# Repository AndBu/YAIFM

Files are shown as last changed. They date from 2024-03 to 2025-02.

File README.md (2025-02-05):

# Yet another IKEA Fridans Motorization (YAIFM)

An affordable, available, easy-to-build drop-in replacement for the orginial “magic wand”. The design has been up and running in my own home for a good half year now and it works without any issues so far. The benefits are:
* Drop-in replacement, i.e. works with the same IKEA wall or ceiling mounts, no new holes or repositioning necessary
* Powered from a regular 5V USB-C power supply
* Works with Home Assistant using ESPHome
* Worldwide availability of components (through Aliexpress and/or other electronics vendors)
* 3D printable on a stock Ender 3

Here are two gifs of how to install the final product:

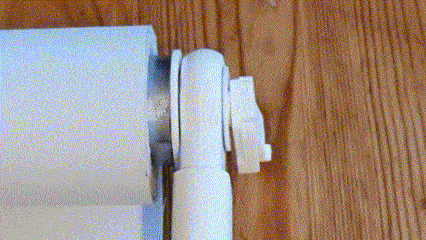
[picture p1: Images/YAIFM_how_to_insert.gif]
How to attach it.

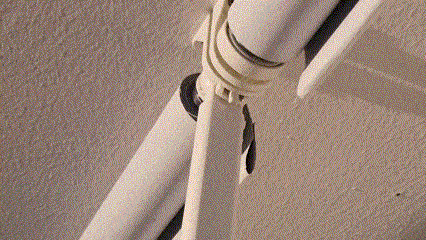
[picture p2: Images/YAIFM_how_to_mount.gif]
How to install it.


And here is a gif of it in action:

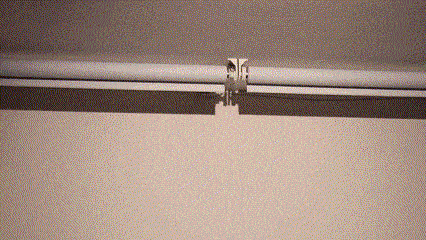
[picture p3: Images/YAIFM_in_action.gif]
How to use it.


Interested? This repository has all you need. The basic steps are simple:
1. Print the parts and assemble the motor holder (screwing required)
2. Assemble the control PCB (soldering required)
3. Flash ESPHome and integrate everything within HomeAssistant
4. Remove the wand, pop in the motor assembly, connect the wires
5. Profit

So you have set you mind on building this things? Awesome! **Be sure to check out the [Limitations and constraints](#limitations-and-constraints) section at the end of this document before you start.**

# Bill of Materials (BOM)

For building one device, you will need to first obtain all the parts on the Bill of Materials (BOM) in the listed quantities. The BOM is separated in to everything needed for the motor assembly as well as everything needed for the control electronics and the wiring.

You can download a Microsoft [Excel file of the BOM here](https://github.com/AndBu/YAIFM/blob/main/BOM/YAIFM%20Bill%20of%20Materials%20(BOM).xlsx).

## Motor assembly BOM

The motor assembly houses the motor and is equipped with an optional wned stop switch to detect the blind's end stop position. **Please be aware, that while a version without an endstop switch exists, I have not yet created a yaml-script for that**. The motor assembly is the part that gets fit into the pipe instead of the "magic wand". The components needed for the motor assembly are listed below:

| Component | Description | Supplier | Alternative | Quantity | Cost (app.) |
| --- | --- | --- | --- | --- | --- |
| Motor holder | Due to the general limitations of FDM 3D printing, the motor assembly is split into multiple parts: the motor holder, the lid and the clip. An optional switch holder can be attached for using en end-stop switch for the blinds. | 3D printed | \- | 1x | \- |
| Motor holder lid | Lid for motor holder. | 3D printed | \- | 1x | \- |
| Motor holder clip | The clip is used to snap the motor assembly in place, much like the original wand. The clip has to be printed in a different orientation for easy printing and maximum mechanical stability, so it is a separate part. | 3D printed | \- | 1x | \- |
| M3x4mm flat head screw | The orignal IKEA Fridans wand is rivited. My clip is screwed onto the motor holder with a flat M3x4mm screw. The screw's maximum head thickness is 1.5mm. You can probably get away with a thicker screw or just glue it. | [Aliexpress](https://www.aliexpress.com/item/1005004288328345.html) | Hardware store | 1x | 1USD (per set) |
| DC motor | GA12-N20 miniature geard DC motor wth integrated rotary encoder, with 39RPM @ 6V supply. Different version of this motor exist with different power and torque rating. In order to reliably drive the widest (200cm) IKEA Fridans blinds, I recommend a motor with a stall torque of at least 0.5Nm and a shaft speed of around 39RPM at no load. Be careful, motors can have different electrical characteristics even though they look the same. The Adafruit motor is slower and on the lower end of the torque spectrum. It won't work reliably for blinds >100cm (and even for the narrower blinds, I have not tested it), but I have included it, because it might be easier to source for some of you. | [Aliexpress](https://www.aliexpress.com/item/4001045242610.html?spm=a2g0o.order_list.order_list_main.196.54af1802pgRf9I) | [Adafruit (not for >100cm blinds!)](https://www.adafruit.com/product/4640) | 1x | 10 USD |
| Hub | The hub sit directly on the motor shaft and transfers the torque from the gearbox to the blind. It should fit rather firmly. I have included multiple parts with different shaft tolerances and I have also included a tolerance tester part so you can choose the right part before printing the whole hub. | 3D printed | \- | 1x | \- |
| Switch holder | Optional. The switch holder secures the limit switch at the correct angle and distance. The switch holder is long because the plastic reinforcement inside the seam of the blind's fabric triggers switch and it can move. If you have an unusually short reinforcement part, for example because you were not careful when cutting your blinds to fit, you might need to make adjustments to this part. | 3D printed | \- | 1x | 5USD (per set) |
| End stop switch | Optional. This switch can can detect when the blind is fully closed. It is triggered by the long plastic reinforcement part inside the seam of the blind. It is mounted usind the 3D printable switch holder. I kept is simple and stupid using one of my spare limit switches for my Ender 3 V2 3D printer. | [Aliexpress](https://nl.aliexpress.com/item/1005003409480909.html) | Any other Creality-like end stop limit switch | 1x | 3USD (per set) |
| M2.5x6mm screw | Optional: This screw is used to mount the switch holder to the motor holder and the switch to the switch holder. If you use the switch holder, you will need these screws. | [Aliexpress](https://www.aliexpress.com/item/1005004288328345.html) | Hardware store | 3x | 1USD (per set) |

## Control PCB

The control PCB drives the motor, reads the rotary encoder for accurate position sensing and connects to your home's WIFI for integrating with HomeAssistant. The components needed for the control PCB are listed the following:

| Component | Description | Supplier | Alternative | Quantity | Cost (app.) |
| --- | --- | --- | --- | --- | --- |
| WeMos D1 MINI | The WeMos D1 MINI is a small ESP8266 powered WIFI-enabled microcontroller board. Many compatible boards exist such as the newer Lolin S2 mini, which comes with a beefier ESP32-S2 processor. If you don't have a WeMos D1 MINI lying around, I'd recommend going for the Lolin S2 mini as it is simply put the much better board, especially since ESP8266 GPIOs do really strange things during bootup. | [Aliexpress](https://www.aliexpress.com/item/1005006018009983.html) | WEMOS D1 mini compatible board from local supplier | 1x | 5USD |
| DC motor driver | The DRV8833 is a common, affordable, low-power motor driver with two independently controllable H-bridges. Different boards from different suppliers exist. You can of course also use any other compatible H-bridge DC motor driver such as the popular MX1508 but watch out for the changed dimensions any pinning. | [Aliexpress](https://aliexpress.com/item/4000083406292.html) | Local electronics supplier | 1x | 1USD |
| Perfboard | I used common perfboard for holding the electronics in place. If you want to use my PCB holder, your perfboard will to be 3cm x 7cm. | [Aliexpress](https://aliexpress.com/item/1005004818919331.html) | Local electronics supplier | 1x | 1USD (per set) |
| Wire | Some wire to connect everything on the underside of the perfboard. | Hardware store | Local electronics supplier | \- | \- |
| 8pin header (male + female) | Optional: I prefer to have the option to remove the WeMos D1 mini as well as the DRV8833 board for debugging purposes. Thus, I do not solder the board to the PCB directly. In order to make the board detachable, you'll need at least two 8pin female pin headers. My WeMos D1 MINI came with male and female headers (the pins of the female headers had to be trimmed as they were too long). | [Aliexpress](https://aliexpress.com/item/4000523047541.html) | Local electronics supplier | 2x | \- |
| 2pin + 6pin header (male) | Optional: You may solder the wires of the motor and the switch directly to the PCB but I don't recommend it. I soldered common 0.1"/2.54mm pin headers to the PCB and used the dupont style female crimpt connectors for the switch and motor wires. You can easily trim rows of pin headers to the required length (but not the female ones). | [Aliexpress](https://aliexpress.com/item/1005002646300836.html) | Local electronics supplier | 1x | 3USD (per set) |

## Cables and plugs BOM

Below wires and plugs for connecting everything are listed:

| Component | Description | Supplier | Alternative | Quantity | Cost (app.) |
| --- | --- | --- | --- | --- | --- |
| 2pin + 6pin crimp connectors (female) | Optional: You may solder the wires of the motor and the switch directly to the PCB but I don't recommend it. I soldered common 0.1"/2.54mm pin headers to the PCB and used the dupont style female crimpt connectors for the switch and motor wires. You can find sets of crimp connectors for little money online. | [Aliexpress](https://aliexpress.com/item/32758380907.html) | Local electronics supplier | 1x | 1USD (per set) |
| 3pin JST XH plug (female) | Optional. If you use the end stop switch, you can make your own (short) cable with some wire and a 3pin JST XH plug that connects to the switch. You can find sets of JST XH (compatible) plugs and sockets for little money online. | [Aliexpress](https://www.aliexpress.com/item/1005001463771344.html) | Local electronics supplier | 1x | 5USD (per set) |
| Crimping pliers | Optional: If you want to crimp Dupont plugs, you'll need a pair of crimping pliers. The ones that I have are both good and inexpensive. | [Aliexpress](https://aliexpress.com/item/4001179493284.html?) | Local electronics supplier | 1x | 20USD |

# Build instructions

Building your own IKEA Fridans motorization system is not hard. The instructions below cover the basic steps - from printing the parts, assembling the control PCB, wiring everything all the way to flashing ESPHome and integrating it in HomeAssistant.

## Printing the parts

All 3D printable parts can be printed using standard PLA. You can download them [from here](https://github.com/AndBu/YAIFM/tree/main/STL). I tested printing on both my BambuLab X1 Carbon as well as my stock Creality Ender 3 V2 Neo using eSun PLA+ and BambuLab filament.

The most critical part is the hub as it must fit tightly on the motor shaft. Slow printing is the key to success. I have included versions of the hub with increased and decreased hole tolerances in case you need it. On both my Ender 3 as well as my BambuLab X1 Carbon, I got the best results using OrcaSlicer with the "Precise wall(experimental)" feature turned on.

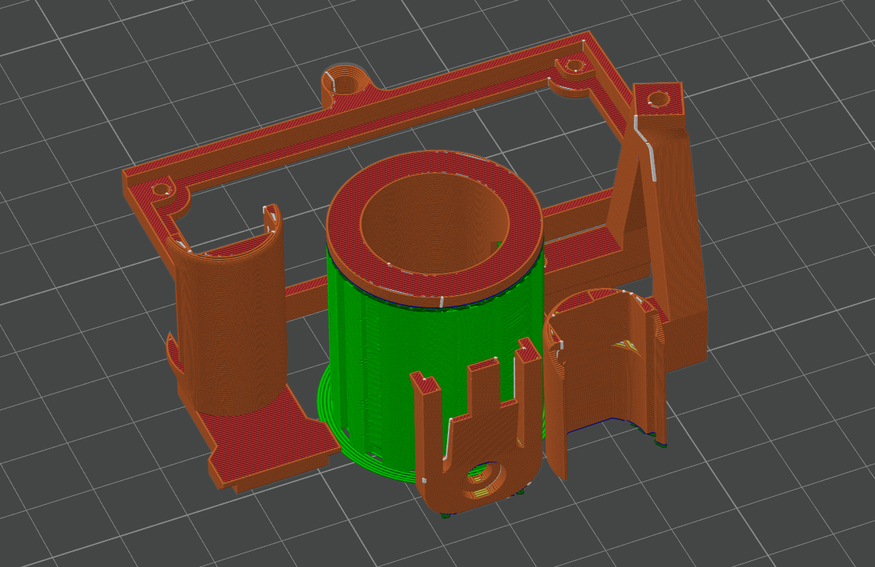
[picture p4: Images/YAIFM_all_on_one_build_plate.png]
Arrangement of parts on a single build plate.


All parts can be printed with the default orientation of the STL files. If you have a printer that can reliably print multiple objects on one build plate, go for it. Should you have trouble printing, here are some tips and tricks:

* **Hub**: needs to be printed standing on its nose. You need support to print the rim on the top. I got the best results using OrcaSlicer with regular supports and snug fit on printbed only. I got best results using OrcaSlicer with the "Precise wall(experimental)" feature turned on and printing in "Silent" mode.
* **Motor holder** needs to be printed with the flat side down. You'll need to enable support for the arm that extends out to the switch holder (if you are using the version with the end stop switch). I got the best results using OrcaSlicer with regular supports and snug fit on printbed only. Again, I printed with the "Precise wall(experimental)" feature turned on.
* **Switch holder**: should be printed standing on the flat surface in the back. Again, I printed with the "Precise wall(experimental)" feature turned on.
* **Clip**: should be printed standing on the rounded end.
* **PCB holder**: should be printed flat on its back.

I cannot stress this enough: Especially on entry-level printers such as the Ender 3, slow printing is key to success. I had no issues with bed adhesion, and I always printed without a brim.

## Putting the motor assembly Together

Putting the motor assembly together is straight forward. Slide the motor into the motor holder, snap the lid on and screw the clip into place with a flathead M3x4mm screw (or glue it on). That's it. If you are using the switch holder, use an M2.5x6mm screw to attach it to the motor holder and screw the end stop switch into place with two of the same screws. The hub needs to be attached to the motor shaft with quite some force. There is a window in the hub with which you can check the correct orientation. Be sure to never push on the PCB or the rotary encoder magnet as this will damage the motor (been there, done that!).

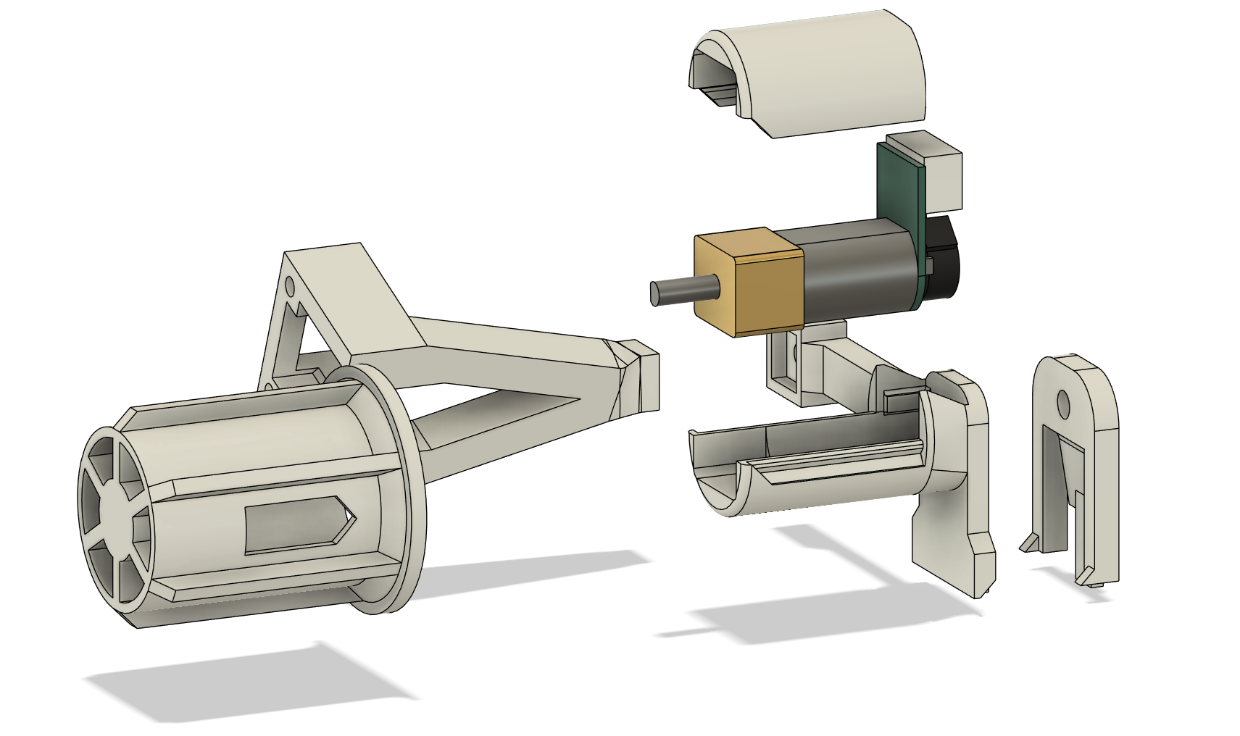
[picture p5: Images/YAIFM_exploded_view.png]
Explosion view of the assembly


## Assembling the control PCB

Assembling the control PCB is straight forward, provided you have basic soldering skills. Here is a circuit diagram to show you how the parts are connected:

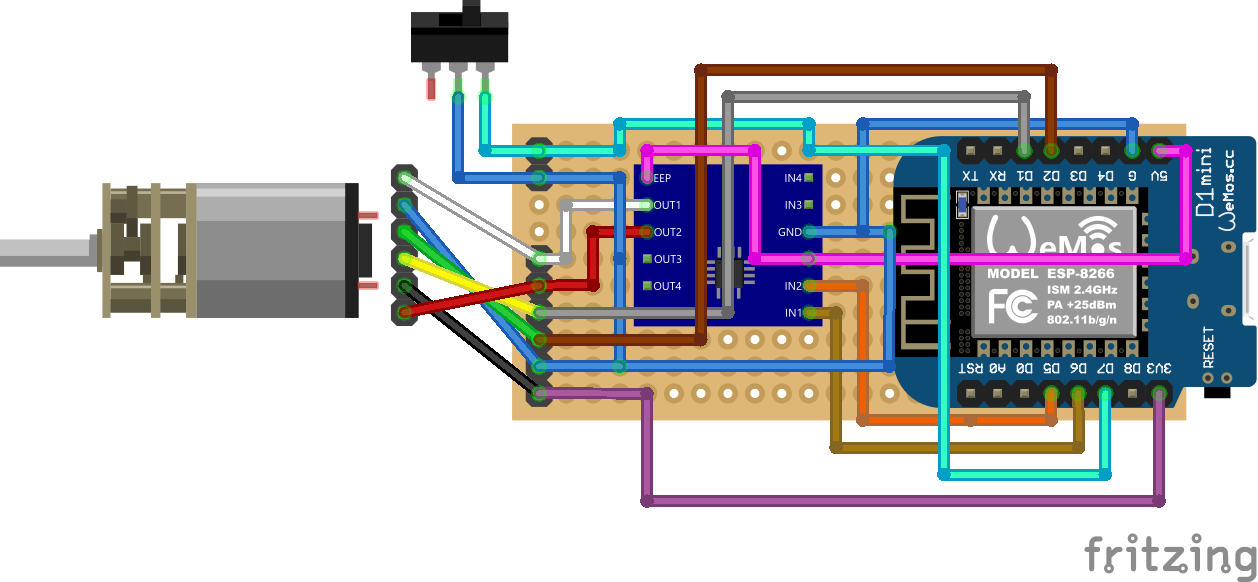
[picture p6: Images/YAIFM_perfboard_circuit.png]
Circuit of the control PCB for assembly on a perfboard.


I recommend the following order of assembly:
* Start with soldering the male pin headers to the WeMos D1 MINI and the DRV8833 motor driver boards.
* Then, attach the female pin headers to the newly soldered male pin headers and insert the WeMos D1 MINI (and later the DRV8833 motor driver) boards onto the perfboard. Solder the female pin headers (with the boards still attached and firmly held into place) to the perfboard.
* Attach the 2pin and 6pin headers for the motor cable and the switch cable in the front of the board.
* Wire everything neatly on the underside of the perfboard.

## Flash ESPHome to the WeMos D1 MINI

Flashing ESPHome on the WeMos D1 MINI is straight forward and plenty of guides exist on the internet. Here is a [video explaining the installation of ESPHome and adding your first device](https://www.youtube.com/watch?v=W0jyPd31J_0) based on the WeMos D1 MINI.

If you are already familiar with ESPHome and just need a refresher, the steps in short are:
* Plug the WeMos D1 MINI directly into your computer with a USB-C cable.
* Navigate to the ESPHome tab in your HomeAssistant installation, click on "+ New Device" in the bottom-right corner of your screen, then click "Open ESPHome Web" and a new site will open.
* Using the ESPHome Web interface click on "Connect" and a dialog window opens. In the dialog window, select the COM port of your device, and click "Connect"
* Follow the instructions to add a minimal ESPHome firmware.
* Navigate back to the ESPHome tab in your HomeAssistant installation and configure the new device.

## Integrate into home assistant

Once you have integrated the device into ESPHome, it is time to configure it. [This sample configuration](/SRC/YAIFM_ESPHome_sample_configuration.yml) is a proof of concept and comes without any warranty.

**As of now, the code will not run if you do not use the end stop switch as it expects a naturally-closed connection of the switch. After every reboot of the WeMos D1 mini, the blind has to be initialized by rolling it all the way to the end first.**

## Custom PCB

You can find a custom PCB in the [PCB folder](PCB/). A description can be found [here](PCB/YADCMCB.md). **The PCB has a different pinout compared to the protoboard.**

# Limitations and constraints

Not sure yet if this design is for you? That's OK. Here are the most important limitations and constraints to help you get a better picture of what you are getting yourself into.

## A word of advice

Mounting home-made stuff to the ceiling can present a safety hazard. Modifying your IKEA blinds (and/or using any of the advice or parts or code in this repository) is done strictly at your own risk. Especially with 3D printed parts, there is always a risk of problems with layer adhesion and/or part fatigue; always make sure you have your print-settings dailed when printing structural parts!

## Missing features

A couple of features are still missing, mainly because I didn't finde the time to write the full softare. Here are the most important issues:
* While you can use the blind without a switch, you will have to write your own yaml script for it. This should be fairly straight forward, but still, you have to do it. The proof-of-concept script that I have attached uses the switch to determine the closed position every time the device starts again as well as everytime the blind gets rolled back up. The rotary encoder is so far only used to determine the open position.
* The blind is currently not capable of moving to an arbitrary position. It can only toggle between open and closed. This is a software limitation, and given the fact that there is a rotary encoder on the motor, this should again be a fairly straight forward implementation.
* The "open" position of the blind is currently still hardcoded in the yaml-script. You'll have to configure the "open" position before using it.
* Variable speed operation is currently not possible. This is again a software limitation. Given the fact that the control board is equipped with a variable-speed H-bridge DC motor controller, implementing various speeds should be straight forward, but I have not done it (yet).

Don't forget, this is a hobby project, so of course, the designs come without any warranty. You are encouraged to support with better software and/or better electrical and mechanical designs.

## Why another IKEA Fridans automation project?

Simply put, I was not satisfied with the size and mechanical complexity of the existing motirisation options:
* [This project by nidayand ](https://www.thingiverse.com/thing:2392856) uses a standard stepper motor with printed gears, which is too bulky for my taste.
* [This project by REALiAM](https://www.thingiverse.com/thing:4889111) uses a direct-drive stepper motor, but it was still too bulky for my purpose.
* [This project by Carly Schulte](https://github.com/charlyschulte/diy-ikea-blinds) is also too bulky for me.

Instead, my goal was to create a drop-in replacement for the "magic wand", meaning I wanted to leave my existing mounts where they are, and just snap-in the motor assembly and be done. I especially wanted to avoid drilling new holes in my ceiling; I could not even reposition the mounts because I have multiple blinds mounted millimeters apart.

## Wow, that sounds too good to be true. Where's the catch?

There might be additional limitations based on your intended usage. Here is what I can think of:
* **Noise**: I am using a geared DC motor, so you can hear the whine of the high speed motor and the rattling of the metal cogs when the blind is moving. The vibrations get somewhat amplified by the plastic housing. Yes, you can reduce the speed, but if you are looking for truly silent operation, you will need to set your sights on another project. Of course, you could also try to work with different motor voltages and speeds and hence different gearboxes (which would require different control electronics), but I wouldn't set my hopes up too high. Maybe adding some tolerance to the motor housing and sleeving the motor with a shrinking hose can dampen the vibrations?
* **No continuous operation**: this will definitely be an issue if you operate the blinds multiple times in a short timeframe. The small motor can create quite some heat and the heat will stay trapped inside the plastic assembly. PLA gets soft at around 50°C so especially in when you live where it gets hot behind your windows, consider printing with a high-temperature polymer like ABS or ASA instead.
* **Calibration**: The more often you roll the blinds up and down, the more crinkled and "thick" the roll becomes. Possibly, this can create an issue with the end stop switch at some point. On the other hand, not using the end stop switch means you might need to recalibrate a couple of times, especially after buying a new roll.
* **IKEA factory tolerances**: None of the blinds I ordered were perfectly straight, so I had to bend them to reduce the stress on the motor. Granted, this is not really a limitation of this setup, just something I encountered.

# Disclaimer

The information contained in this repository is for general information purposes only. The information is provided by the contributors who make no representations or warranties of any kind, express or implied, about the completeness, accuracy, reliability, suitability or availability for any purpose, including but not limited to information, products, services, or related graphics. Any reliance you place on such information is therefore strictly at your own risk.

Also, the contributors are not affiliated with any of the shops or brands linked and discussed here. While they might have successfully tested the components in their own designs, they do not recommend any specific component from any manufacturer or shop in particular. Information about shops or products or manufacturers, including but not limited to links, are for illustrative purposed only. Manufacturers or distributors of electrical components are known to change a product's specification without notice.

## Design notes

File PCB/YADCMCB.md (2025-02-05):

# Yet Another DC Motor Control Board (YADCMCB) [v0.9]

This PCB can be used for controlling the motor of Yet Another IKEA Fridans Motorization (YAIFM). The design goal of the PCB was to make assembly quick and easy, using readily available PCB modules such as the DRV8833 DC motor controller (or the DC MX1508 motor controller) and the Wemos D1 Mini ESP8266 board (or the Wemos S2 Mini ESP32 board).

**The board is currently in testing. Not all functions are tested.**

**THE PINOUT OF THE BOARD IS DIFFERENT FROM THE PINOUT OF THE PROTOBOARD FOR THE YAIFM Project**

A typical motor to control with this board is the [GA12-N20 geared DC/DC motor](https://www.aliexpress.com/item/4001045242610.html).

## Motor controllers

The board is designed to fit either a [DRV8833](https://aliexpress.com/item/4000083406292.html)  DC motor controller or an [MX1503](https://www.aliexpress.com/item/1005006750110807.html) DC motor controller. However, the board only makes use of one of their channels and obviously, only one board can be fitted at once.

## Pinout

The board has 8 outputs, of which 2 are hardwired to ground and one is hardwired to the 3.3V supply of the Wemos D1 Mini:
- W: OUT1 of the DRV8833 (or MX1508 if used)
- R: OUT2 of the DRV8833 (or MX1508 if used)
- Y: SCL/D1 of the Wemos D1 Mini
- K: 3.3V
- G: SDA/D2 of the Wemos D1 Mini
- B: GND
- S: MISO/D7 of the Wemos D1 Mini

The first 6 letters in the above table correspond to the wire colors of the [GA12-N20 geared DC/DC motor](https://www.aliexpress.com/item/4001045242610.html) (last check: Feb 2025). Output "S" is a GPIO where e.g. and endstop switch can be connected.

The 3.3V supply of the Wemos D1 Mini cannot source a lot of current (it's an LDO connected to 5V). Don't use it for powering anything more than ICs or low-power LEDs.

## USB-C Decoy + POL Option

The board can fit [this USB-C decoy](https://www.aliexpress.com/item/1005008134795923.html) on the top layer. Together with this [non-isolated DC/DC (POL "Point of Load") converter](https://www.aliexpress.com/item/1005006005553178.html) (**choose the version with an output voltage of 5V when you order!**), the user can operate the Motor at a voltage of 9V (or 12V, but this is out of spec for the DRV8833 and MX1503) when plugged into a compatible USB-C power source.

When the USB-C decoy board and the POL are fitted, the Wemos D1 Mini is powered from the voltage provided by the POL and the motor is powered from the negotiated USB-C input voltage. **JP1 must be open if your are using the USB-C decoy.**

**Do not power the board from the USB-C decoy and the USB-C port on the Wemos D1 Mini at the same time.**

## INA 219 Option

The board allows for fitting INA219 current sensor board, inserted into the supply current path of the motor controller PCB. The current sensor can be used to detect motor stalling or measure output power. The response of the sensor is limited by the input capacitance of the motor controller PCB.

This options is not yet tested or documented. **When no INA219 current sensor board is fitted, JP2 must be closed.**

## Jumpers

The board has two jumpers:

- **JP1** shorts the output of the USB-C decoy (which is wired to the supply of the motor control PCB) with the 5V rail of on the Wemos D1 Mini. **When using a USB-C decoy board, JP1 must remain open.**
- **JP2** shunts the current-sensing path of the INA219. **When no INA219 current sensor board is fitted, JP2 must be closed.**

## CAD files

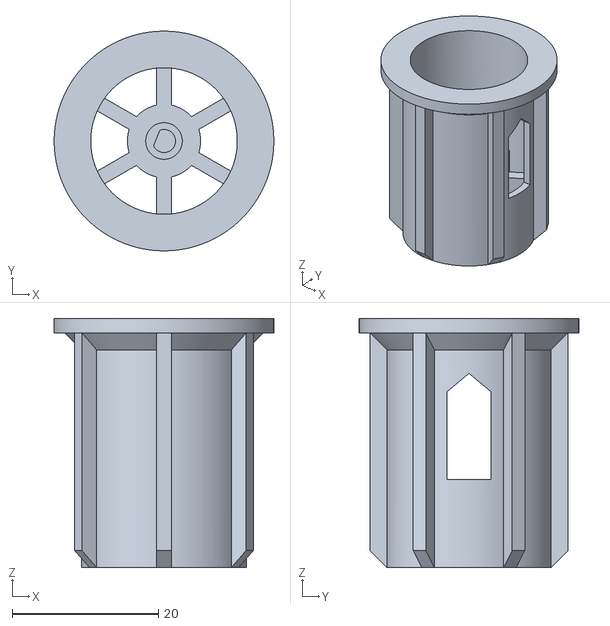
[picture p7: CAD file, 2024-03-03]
STL/different_hub_hole_clearances/YAIFM_hub_minus_0.05mm_hole_clearance.stl
30.0 x 30.0 x 34.0

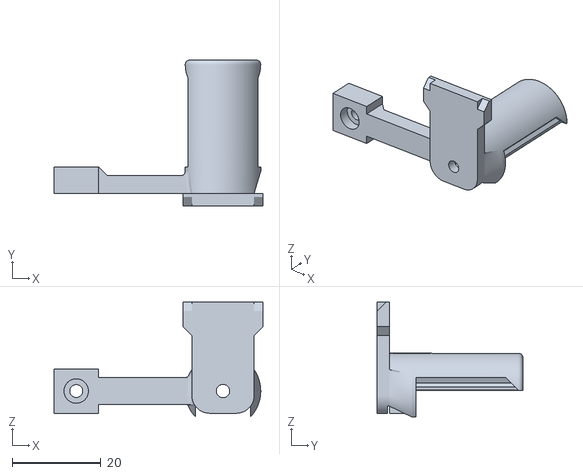
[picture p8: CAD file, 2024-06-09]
STL/motor_holder_for_switch_holder.stl
47.0 x 32.8 x 25.8

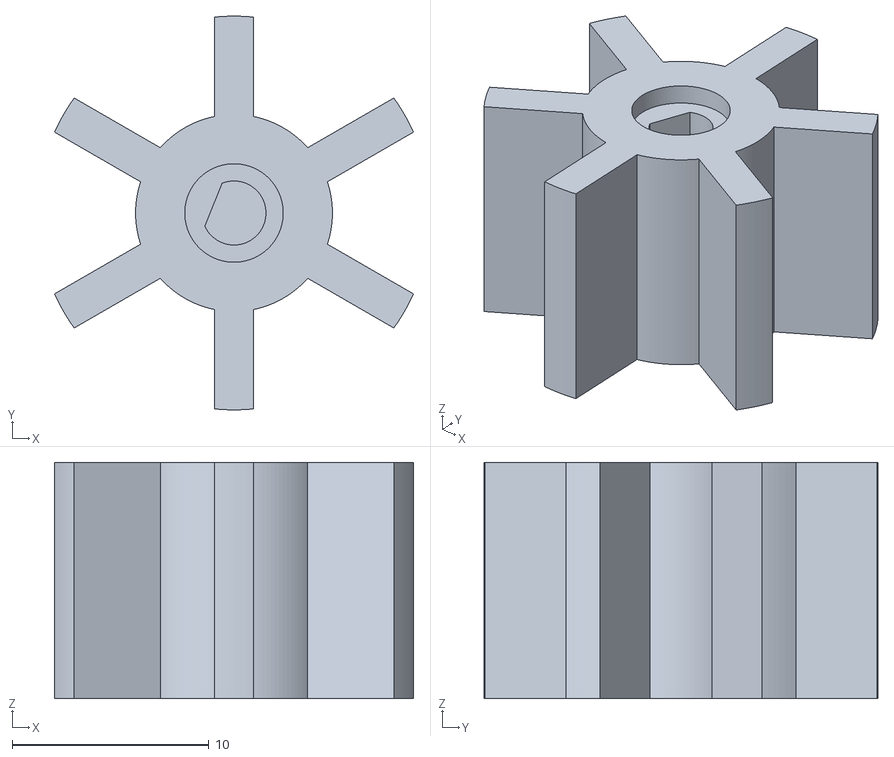
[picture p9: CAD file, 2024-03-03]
STL/different_hub_hole_clearances/YAIFM_tolerance_checker__hub_plus_0.05mm_hole_clearance.stl
18.2 x 20.0 x 12.0

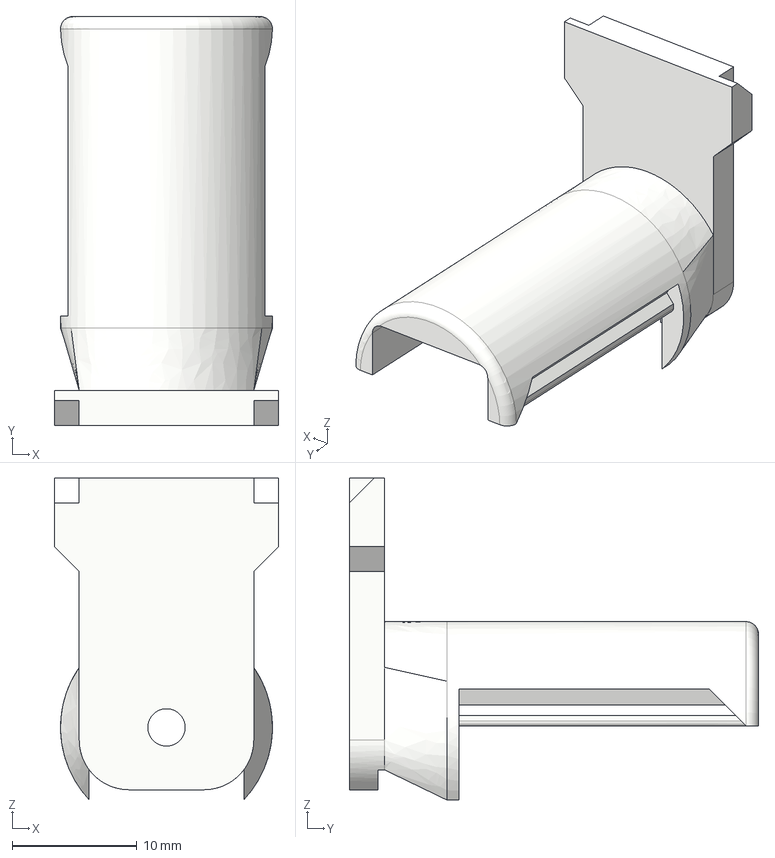
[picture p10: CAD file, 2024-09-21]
STP/YAIFM_motor_holder.step
18.0 x 32.8 x 25.8 mm

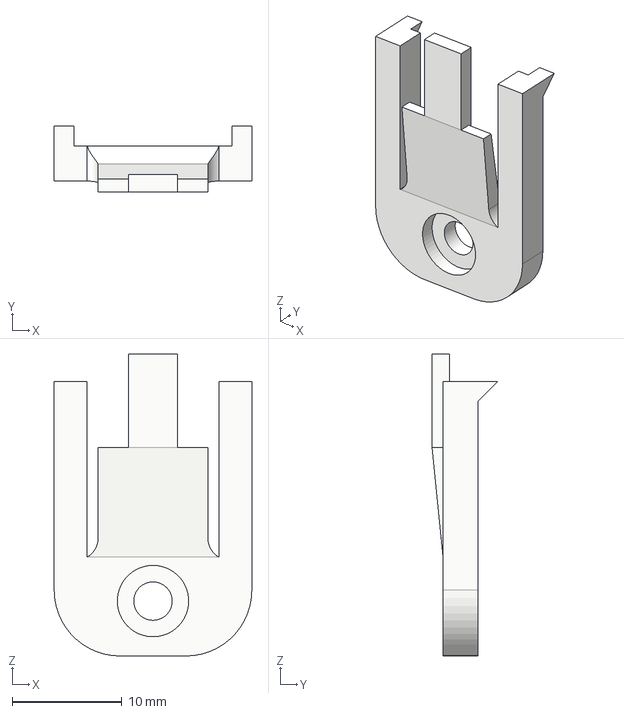
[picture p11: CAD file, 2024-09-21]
STP/YAIFM_clip.step
18.0 x 6.00 x 27.5 mm

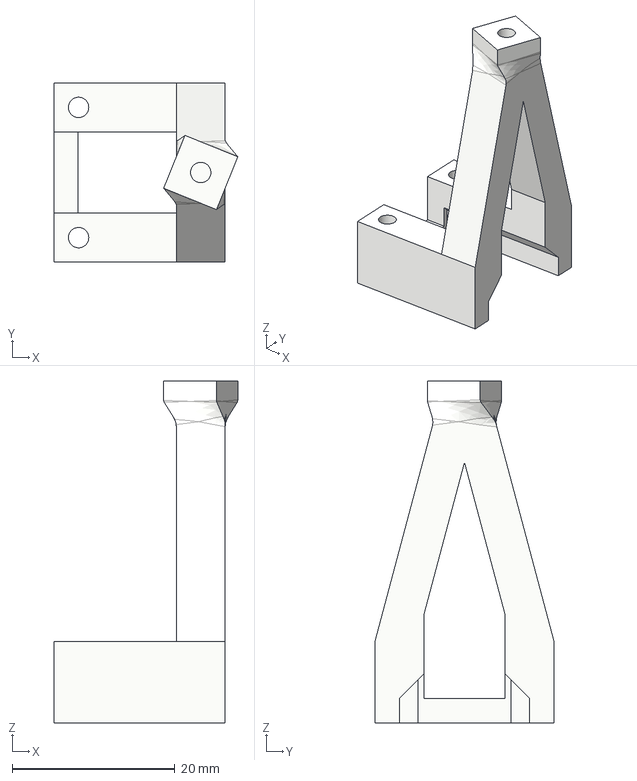
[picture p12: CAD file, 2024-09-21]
STP/YAIFM_switch_holder.step
22.6 x 22.0 x 42.0 mm

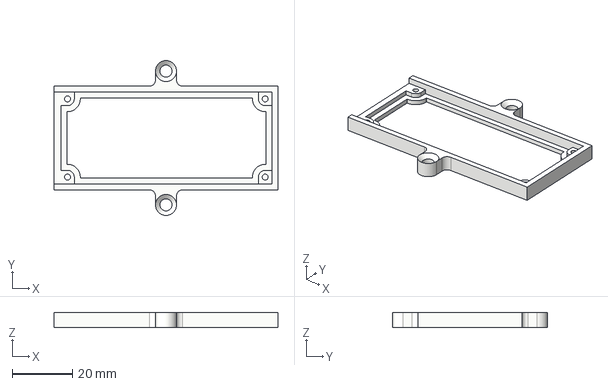
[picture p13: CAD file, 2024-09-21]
STP/YAIFM_PCB_holder.step
74.5 x 51.5 x 5.00 mm

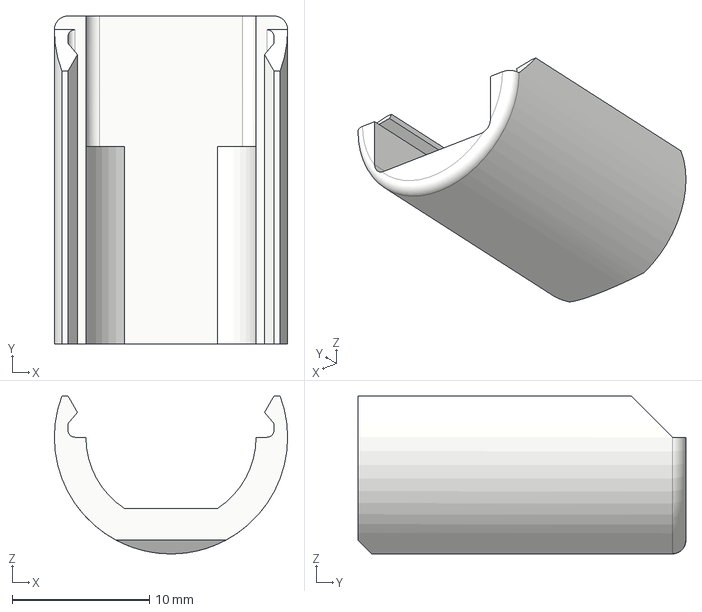
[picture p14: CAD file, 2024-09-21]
STP/YAIFM_lid.step
17.0 x 23.9 x 11.5 mm

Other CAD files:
STP/YAIFM_hub.step
STL/YAIFM_tolerance_checker__hub.stl
STP/YAIFM_motor_holder_for_switch_holder.step
STL/different_hub_hole_clearances/YAIFM_tolerance_checker__hub_minus_0.05mm_hole_clearance.stl
STL/different_hub_hole_clearances/YAIFM_hub_plus_0.05mm_hole_clearance.stl
STL/different_hub_hole_clearances/YAIFM_hub_plus_0.1mm_hole_clearance.stl
STL/different_hub_hole_clearances/YAIFM_tolerance_checker__hub_plus_0.1mm_hole_clearance.stl
STL/YAIFM_PCB_holder.stl
STL/YAIFM_clip.stl
STL/YAIFM_hub.stl
STL/YAIFM_lid.stl
STL/YAIFM_motor_holder.stl
STL/YAIFM_switch_holder.stl

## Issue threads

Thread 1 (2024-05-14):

Motor holder with Switchmount missing

zenzmatz, 2024-05-14:
Hi,

In the Mockup of all 3D-Printed parts, and in the "Printing parts section" you are mention YAIFM_motor_holder.stl with an mount for the YAIFM_switch_holder.stl, but it looks like, you didn't uploaded it yet.

Could you upload this file?

shawru, 2024-06-06:
Also noticed this, did you get any update?

AndBu, 2024-06-06:
Sorry, slipped my attention. Will upload on the weekend :)

AndBu, 2024-06-09:
Uploaded.

Closed 2024-06-09.

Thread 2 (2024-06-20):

Provide step-files for 3D-printed parts

benbender, 2024-06-20:
Hey,

first and foremost: Very nice project! Thank you for putting in the work and sharing the results!

I'm in the process of replicating the project and started with 3d-printing parts and sourcing materials.
To make it perfectly fit for my circumstances I would like to do some modifications like having a closed box für the electronics.
To do this, it would be quite helpful to have the step-files for the 3d-prints so I don't have to measure myself and reinvent the wheel.

Could you provide those?

AndBu, 2024-09-21:
Thanks for the comment. I have now uploaded the step files as well.

benbender, 2024-09-22:
Thank you very much! <3

AndBu, 2024-09-22:
I could also upload the Fusion design files if that helps but they might need some cleaning up to be really useful.

Closed 2024-09-21.

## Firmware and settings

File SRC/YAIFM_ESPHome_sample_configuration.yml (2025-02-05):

#Copyright (c) 2024 AndBu and others
#
#Permission is hereby granted, free of charge, to any person obtaining
#a copy of this software and associated documentation files (the
#"Software"), to deal in the Software without restriction, including
#without limitation the rights to use, copy, modify, merge, publish,
#distribute, sublicense, and/or sell copies of the Software, and to
#permit persons to whom the Software is furnished to do so, subject to
#the following conditions:
#
#The above copyright notice and this permission notice shall be
#included in all copies or substantial portions of the Software.
#
#THE SOFTWARE IS PROVIDED "AS IS", WITHOUT WARRANTY OF ANY KIND,
#EXPRESS OR IMPLIED, INCLUDING BUT NOT LIMITED TO THE WARRANTIES OF
#MERCHANTABILITY, FITNESS FOR A PARTICULAR PURPOSE AND
#NONINFRINGEMENT. IN NO EVENT SHALL THE AUTHORS OR COPYRIGHT HOLDERS BE
#LIABLE FOR ANY CLAIM, DAMAGES OR OTHER LIABILITY, WHETHER IN AN ACTION
#OF CONTRACT, TORT OR OTHERWISE, ARISING FROM, OUT OF OR IN CONNECTION
#WITH THE SOFTWARE OR THE USE OR OTHER DEALINGS IN THE SOFTWARE.

#This is a proof-of-concept automation template for the YAIFM
#"Yet another IKEA Fridans Motoriozation Project"
#
#The source can be found on GitHub:https://github.com/AndBu/YAIFM
#
#This script assumes you have a Wemos D1 Mini ESP8266 board. If you
#have another board, change the board type and pin assigment. On an 
#ESP32 board, it is recommended to switch to the hardware PWM as 
#described here: https://esphome.io/components/output/ledc
#
#This script requires the end stop switch, if you don't want to use the
#end stop switch, write your own script and share it please ;)

esphome:
  name: <your_device_name>
  friendly_name: <your_friendly_name>
  on_boot:
    priority: 600
    # This ensures that the blind has to be pulled up and hit the limit switch on the first boot
    then:
      - cover.template.publish:
          id: screen
          state: CLOSED
          current_operation: IDLE
      - sensor.rotary_encoder.set_value:
          id: re_mot
          value: 0      
esp8266:
  board: d1_mini 

# Enable Home Assistant API
api:
  encryption:
    key: <your_device_key>

ota:
  password: <your_password_name>

wifi:
  ssid: !secret wifi_ssid
  password: !secret wifi_password

  # Enable fallback hotspot (captive portal) in case wifi connection fails
  ap:
    ssid: <your_hotspot_fallback_ssid>
    password: <your_hotspot_fallback_password>

# Disable logging via serial since we are using the pins of the serial port
logger:
  baud_rate: 0

# Configure the pins for PWM
output:
  # Blinds (+) and (-) leads for motor
  - platform: esp8266_pwm
    id: mot_m1
    pin: GPIO14 #D6 on te WeMos D1 MINI  
  - platform: esp8266_pwm
    id: mot_m2
    pin: GPIO12 #D5 on te WeMos D1 MINI


binary_sensor:
  # End stop
  - platform: gpio
    id: sw_mot
    name: "End Stop"
    internal: True
    pin:
      number: 13 #D7 on te WeMos D1 MINI
      inverted: true
      # The end stop  switch is naturally closed.
      # If there is an open circuit (i.e. broken connection),
      # we want that to be detected, hence the pullup)
      mode:
        input: true
        pullup: true

sensor:
- platform: rotary_encoder
  name: "Motor encoder"
  internal: False
  id: re_mot
  pin_b: GPIO4  #D2 on te WeMos D1 MINI
  pin_a: GPIO5  #D1 on te WeMos D1 MINI
- platform: template
  name: "Initialized"
  lambda: |-
    return id(init_done);
  update_interval: 0.1s

fan:
  # Motor controller
  - platform: hbridge
    id: mot
    name: "Motor"
    internal: True
    pin_a: mot_m1
    pin_b: mot_m2
    decay_mode: slow

globals:
  - id: init_done
    type: bool
    restore_value: yes
    initial_value: 'false'
  - id: min_value
    type: int
    restore_value: yes
    initial_value: '0'
  - id: max_value
    type: int
    restore_value: yes
    initial_value: '23000'

number:
  - platform: template
    name: "Screen Minimum Value"
    id: screen_min_value
    optimistic: True
    restore_value: True
    initial_value: 0
    min_value: 0
    max_value: 50000
    step: 100
    set_action:
      - lambda: |-
          ESP_LOGI("set_min_value", "Setting min_value to %d", (int)x);
          id(min_value) = (int)x;

  - platform: template
    name: "Screen Maximum Value"
    id: screen_max_value
    optimistic: true
    restore_value: True
    initial_value: 23000
    min_value: 0
    max_value: 50000
    step: 100
    set_action:
      - lambda: |-
          ESP_LOGI("set_max_value", "Setting max_value to %d", (int)x);
          id(max_value) = (int)x;
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

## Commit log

2024-06-09 Added motor holder for use with switch holder (forgot to add in initial commit)
    [motor_holder_for_switch_holder.stl]
2024-09-21 Added step files to make modding and derivative works easier.
    [YAIFM_PCB_holder.step, YAIFM_clip.step, YAIFM_hub.step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]
2025-01-25 Update README.md
    Updated recommendations on the motor:
    - No longer recmonneding Adafruit motor for blinds wider >100cm
    - No longer recommending Aliexpress motors with >39RPM (suitable for all blinds)
2025-01-25 Various improvements (#3)
    * added user controllable minimum and max values for the top and bottom
    * modified open script so that it stops at the minimum instead of waiting for the switch
    * added 'initialize' button that sets the stepper motor to 0, so it can be calibrated only once
    * dynamically calculate open % based on difference between min and max
    * added script to open/close to specified %
    * added retain value
2025-01-25 - Prevented operating an uninitialized blind - Set initial min value to zero
    [YAIFM_ESPHome_sample_configuration.yml]
2025-02-05 Added Custom PCB
    [YADCMCB-B_Cu.gbl, YADCMCB-B_Mask.gbs, YADCMCB-B_Paste.gbp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]
2025-02-05 Added link to PCB description.
